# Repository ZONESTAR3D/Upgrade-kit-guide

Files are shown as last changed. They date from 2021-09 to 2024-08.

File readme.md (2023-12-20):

### :globe_with_meridians: Choose Language (Translated by google)
(https://github-com.translate.goog/ZONESTAR3D/Upgrade-kit-guide?_x_tr_sl=en&_x_tr_tl=es)
(https://github-com.translate.goog/ZONESTAR3D/Upgrade-kit-guide?_x_tr_sl=en&_x_tr_tl=pt)
(https://github-com.translate.goog/ZONESTAR3D/Upgrade-kit-guide?_x_tr_sl=en&_x_tr_tl=fr)
(https://github-com.translate.goog/ZONESTAR3D/Upgrade-kit-guide?_x_tr_sl=en&_x_tr_tl=de)
(https://github-com.translate.goog/ZONESTAR3D/Upgrade-kit-guide?_x_tr_sl=en&_x_tr_tl=it)
(https://github-com.translate.goog/ZONESTAR3D/Upgrade-kit-guide?_x_tr_sl=en&_x_tr_tl=sv)
(https://github-com.translate.goog/ZONESTAR3D/Upgrade-kit-guide?_x_tr_sl=en&_x_tr_tl=pl)
(https://github-com.translate.goog/ZONESTAR3D/Upgrade-kit-guide?_x_tr_sl=en&_x_tr_tl=da)
(https://github-com.translate.goog/ZONESTAR3D/Upgrade-kit-guide?_x_tr_sl=en&_x_tr_tl=cs)
(https://github-com.translate.goog/ZONESTAR3D/Upgrade-kit-guide?_x_tr_sl=en&_x_tr_tl=hr)
(https://github-com.translate.goog/ZONESTAR3D/Upgrade-kit-guide?_x_tr_sl=en&_x_tr_tl=ro)
(https://github-com.translate.goog/ZONESTAR3D/Upgrade-kit-guide?_x_tr_sl=en&_x_tr_tl=sk)

(https://github-com.translate.goog/ZONESTAR3D/Upgrade-kit-guide?_x_tr_sl=en&_x_tr_tl=ru)
(https://github-com.translate.goog/ZONESTAR3D/Upgrade-kit-guide?_x_tr_sl=en&_x_tr_tl=ja)
(https://github-com.translate.goog/ZONESTAR3D/Upgrade-kit-guide?_x_tr_sl=en&_x_tr_tl=ko)
(https://github-com.translate.goog/ZONESTAR3D/Upgrade-kit-guide?_x_tr_sl=en&_x_tr_tl=id)
(https://github-com.translate.goog/ZONESTAR3D/Upgrade-kit-guide?_x_tr_sl=en&_x_tr_tl=th)
(https://github-com.translate.goog/ZONESTAR3D/Upgrade-kit-guide?_x_tr_sl=en&_x_tr_tl=vi)
(https://github-com.translate.goog/ZONESTAR3D/Upgrade-kit-guide?_x_tr_sl=en&_x_tr_tl=iw)
(https://github-com.translate.goog/ZONESTAR3D/Upgrade-kit-guide?_x_tr_sl=en&_x_tr_tl=ar)
(https://github-com.translate.goog/ZONESTAR3D/Upgrade-kit-guide?_x_tr_sl=en&_x_tr_tl=tr)
(https://github-com.translate.goog/ZONESTAR3D/Upgrade-kit-guide?_x_tr_sl=en&_x_tr_tl=el)
(https://github-com.translate.goog/ZONESTAR3D/Upgrade-kit-guide?_x_tr_sl=en&_x_tr_tl=pt)
(https://github-com.translate.goog/ZONESTAR3D/Upgrade-kit-guide?_x_tr_sl=en&_x_tr_tl=zh-CN)

-----
# ZONESTAR 3D printer upgrade kits / parts 
## :file_folder: [Automatic Repeat Printing Module](./Auto_Repeat_Printing/) 
By upgrading this module to make your 3D printer capable of continuous automatic mass production, only for Z9 series 3d printers.   
[:book: **Use Guide**](./Auto_Repeat_Printing/readme.md)    
[:gift: **Sell Link**](https://www.aliexpress.com/item/1005003767078457.html) 

## :file_folder: [Bed Leveling Sensor](./Bed_Leveling_Sensor/)
[:book: **View details**](./Bed_Leveling_Sensor/)
Hot bed tilt / uneven surface is a common problem of 3D printer, however, the first layer is very important for the successfully print. The main solution to slove this problem is to use a ***bed leveling sensor*** to measure the distance between the nozzle with the hot bed, to generate a ***"hot bed height table"***, and save it in the memory of the 3D printer. While printing, automatically adjust the height of the nozzle to compensate the uneven hot bed. For more information on this issue, please refer to [**Marlin documents - Automatic Bed Leveling**](https://marlinfw.org/docs/features/auto_bed_leveling.html)    
**There are several types of bed leveling sensor:**      
- **PL-08N** is a proximity sensor, it can probing metal hotbed. If your hot bed surface is metal, such as aluminum plate + hot bed adhesive tape, aluminum plate + magnetic hot bed paste, elastic rigid hot bed, etc., you can use this sensor.[:gift: **Sell Link**](https://www.aliexpress.com/item/4000596309710.html)      
- **BLtouch(3DTouch)** is a "famous" bed auto leveling sensor for 3D Printers, it integrates a simple servo motor and an electromagnetic sensor into a very small volume. It can be used for all types of heat beds with high accuracy. The disadvantage is that the wiring and use are a little complex. [:gift: **Sell Link**](https://www.aliexpress.com/item/1005001464420529.html)   
- **ZL-Sensor** is a special photoelectric sensor made by ZONESTAR, it can probing almost all meterial hotbed, also it is easier to wiring such as PL-08N. [:gift: **Sell Link**](https://www.aliexpress.com/item/1005002865311470.html)  

## :file_folder: [Direct Drive Extruder](./Direct_Drive_Extruder/)
[:book: **View details**](./Direct_Drive_Extruder/)    
By using the direct drive extruder, the printer can print flexible filament (e.g. TPU filament) and get better printing quality.   
[:book: **Use Guide**](./Direct_Drive_Extruder/readme.md)   
[:gift: **Sell Link**](https://www.aliexpress.com/item/1005002847644867.html) 

## :file_folder: [Dual Gear Extruder](./Dual_Gear_Extruder/) 
The double gear extruder increases the force of filament feeding, which can effectively reduce the probability of printing defects and failures caused by filament slipping on the extruder.     
[:book: **View details**](./Dual_Gear_Extruder/)   
[:gift: **Full Metal Dual Gear Extruder**](https://www.aliexpress.com/item/1005005868564130.html) 
[:gift: **Dual Gear Extruder**](https://www.aliexpress.com/item/1005003473360998.html) 
[:gift: **4PCS/LOT Dual Gear Extruder**](https://www.aliexpress.com/item/1005006240027747.html) 

## :file_folder: [Filament Run Out Sensor (FROD)](./FROD/)
[:book:**View details**](./FROD/)
Filament run out sensor use a switch to check for the presence of filament in the feeder. If the filament spool runs out, the 3d printer will pause print and wait  you to replace a new spool.   
[**View details**](https://www.aliexpress.com/item/4001309957376.html)  

## :file_folder: [HOTENDs](./HOTEND/)
[:book: **View details**](./HOTEND/readme.md)  
ZONESTAR has been promoting the development of color FDM 3D printing technology, we have introduced different types of hot ends to meet the needs of multi-color printing.  
- **R3 (3-IN-3-OUT) Hotend**[:book: **Use Guide**](./HOTEND/R3/) [:gift: **Sell Link**](https://www.aliexpress.com/item/1005001275429959.html)  
- **M2P1 (3-IN-2-OUT Mix Color) Hotend**[:book: **Use Guide**](./HOTEND/M2P1/) [:gift: **Sell Link**](https://www.aliexpress.com/item/1005001275429959.html)  
- **M3 (3-IN-1-OUT Mix Color) Hotend**[:book: **Use Guide**](./HOTEND/M3/) [:gift: **Sell Link**](https://www.aliexpress.com/item/1005001275429959.html)  
- **M4 (4-IN-1-OUT Mix Color) Hotend**[:book: **Use Guide**](./HOTEND/M4/) [:gift: **Sell Link**](https://www.aliexpress.com/item/1005002124027691.html)  
- **E4 (4-IN-1-OUT Non-Mix Color) Hotend**[:book: **Use Guide**](./HOTEND/E4/) [:gift: **Sell Link**](https://www.aliexpress.com/item/1005002951777699.html)  

## :file_folder: [Laser Engraving](./Laser_Engraving/)
[:book: **View details**](./Laser_Engraving/)
By add a laser engrave engine , you can turn your 3D printer into a simple laser engraving machine.   
[:book: **Use Guide**](./Laser_Engraving/)   
[:gift: **Sell Link**](https://www.aliexpress.com/item/4001309902136.html)

## :file_folder: [Motor Drive Module](./Motor_Driver/)
[:book: **View details**](./Motor_Driver/)
TMC motor drive module used stealthChop2 ultra-quiet technology, it can After upgrading it, the noise of 3D printer stepper motor operation can be significantly reduced.   
[:book: **Use Guide**](./Motor_Driver/How_to_install_Motor_Driver_Module.pdf)  
[:gift: **TMC2208**](https://www.aliexpress.com/item/4000596369015.html) [:gift: **TMC2209**](https://www.aliexpress.com/item/1005001664336751.html) [:gift:**TMC2225**](https://www.aliexpress.com/item/1005003270721219.html)   

## :file_folder: [TFT-LCD](./TFT-LCD)
[:book: **View details**](./TFT-LCD/readme.md)    
[:gift: **Sell Link**](https://www.aliexpress.com/item/1005002378065646.html)  

## :file_folder: [WiFi Module](./WiFi/)
By upgrading the WiFi module, you can  control your 3d printer by wireless. It can work with ZM3E4 and ZM3E2 3D printer control board.   
<!-- [:book:**View details**](./WiFi/)     -->
[:book: **Use Guide**](./WiFi/WiFi_User_Guide.md)    
[:gift: **Sell Link**](https://www.aliexpress.com/item/1005002378551489.html)  

## :file_folder: [Z9V5 500x500 upgrade kit](./Z9V5_500x500/)
Upgrade the build volume of Z9V5 to 500x500x400mm.   
[:book: **View details**](./Z9V5_500x500/readme.md)     
[:gift :**Sell Link**](https://www.zonestar3dshop.com/products/zonestar-z9v5-500x500mm-large-printing-size-upgrade-kit-parts)  

## :file_folder: [Z9V5 linear rail upgrade kit](./Z9V5_LinearRail/)
Upgrade Z9V5 to linear rail.   
[:book: **View details**](./Z9V5_LinearRail/readme.md)     
[:gift: **Sell Link - Offical Store**](https://www.aliexpress.com/item/1005005599988527.html)  [:gift: **Sell Link - Aliexpress**](https://www.zonestar3dshop.com/products/new-arrival-z9v5pro-3d-printer-linear-rail-upgrade-kit-for-zonestar-z9v5pro-mgn9h-slider-3d-printer-parts)

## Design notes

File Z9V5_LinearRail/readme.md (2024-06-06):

### <a id="choose-language">:globe_with_meridians: Choose language </a>









<!-- [![](../lanpic/SW.png)](#sv)
[![](../lanpic/PL.png)](#pl)
[![](../lanpic/DK.png)](#da)
[![](../lanpic/CZ.png)](#cs)
[![](../lanpic/HR.png)](#hr)
[![](../lanpic/RO.png)](#ro)
[![](../lanpic/SK.png)](#sk)
[![](../lanpic/ID.png)](#id)
[![](../lanpic/TH.png)](#th)
[![](../lanpic/VN.png)](#vi)
[![](../lanpic/IL.png)](#iw)
[![](../lanpic/SA.png)](#ar)
[![](../lanpic/TR.png)](#tr)
[![](../lanpic/GR.png)](#el)
[![](../lanpic/BR.png)](#pt)
[![](../lanpic/CN.png)](#zh) -->

----
# <a id="en">Z9V5 Linear Rail Upgrade Kit Installation Guide</a>
### :warning: ATTENTION PLEASE :warning:
Do not slide the slider out of the linear rail, otherwise the balls will slide out of the slider and damage the slider.     
### Video Tutorial
(https://www.youtube.com/watch?v=YjfuKJFiPd4)

## Parts
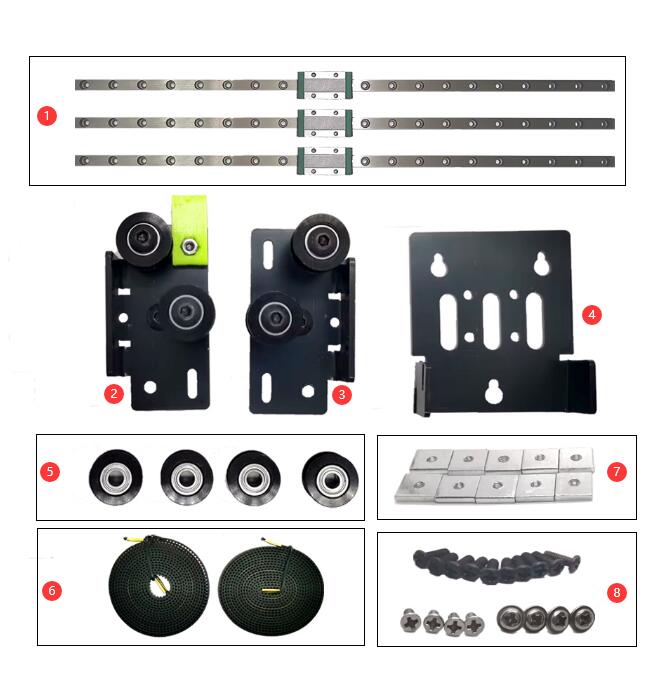
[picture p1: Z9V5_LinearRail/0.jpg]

>
    1. linear rail with slider    2. Y carrier(right)     3. Y carrier(left)      4. X Carrier Metal sheet
    5. Idlers                     6. Belts                7. 10x10 square nut     8. Screws

## Installation
### 1. Take down the hot end (print head) from the X carrier.
Loosen the screws which fixed the print head on the X carrier and take down the print head.   
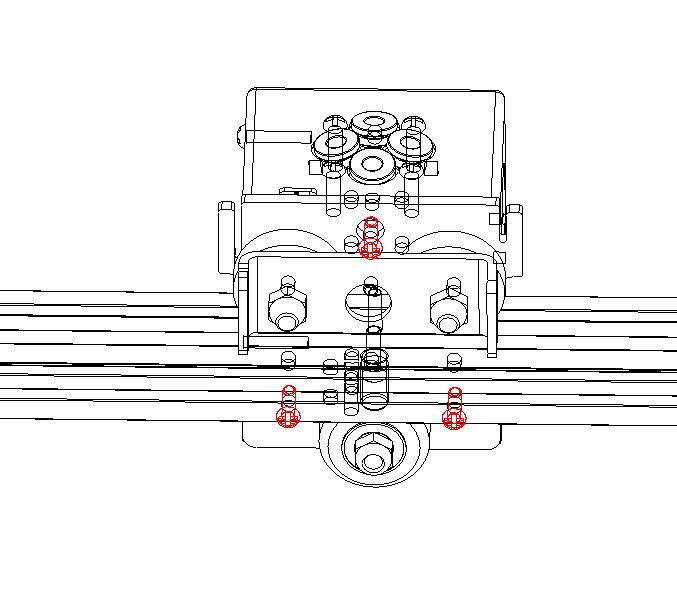
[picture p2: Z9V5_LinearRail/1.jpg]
###### 
### 2. Remove the belts.
### 3. Replace idlers.
Take down the idlers from the front-top profile and replace with the new idlers.    
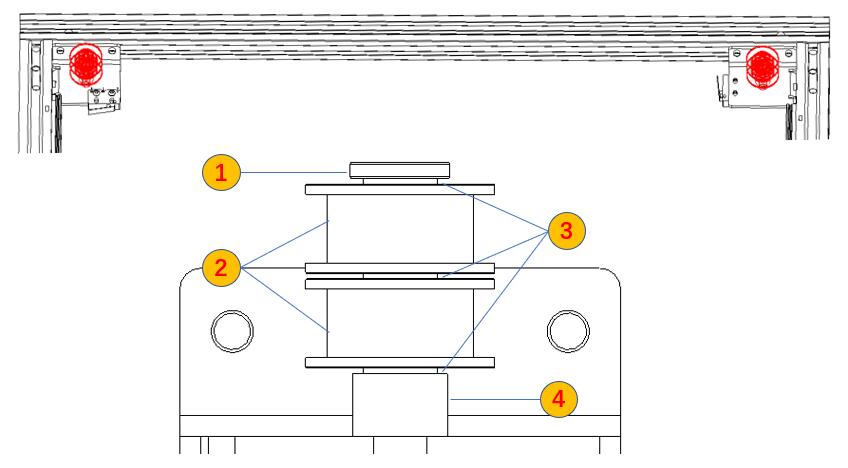
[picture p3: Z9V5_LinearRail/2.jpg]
###### 
>
    1. Screws (use the original one)     2. New idler wheels     3. New shim  4. Pole (use the orignal one)
  :warning: **Note:**
  - Do not tighten the screws too tightly.
  - There may be differences in the elevation columns of different versions of machines.

### 4. Take down the front-top profile.
Remove the screws shown on picture below to take down the front-top profile. **Note**the screw shown in Figure 3 only exists in the nearest Z9V5.  
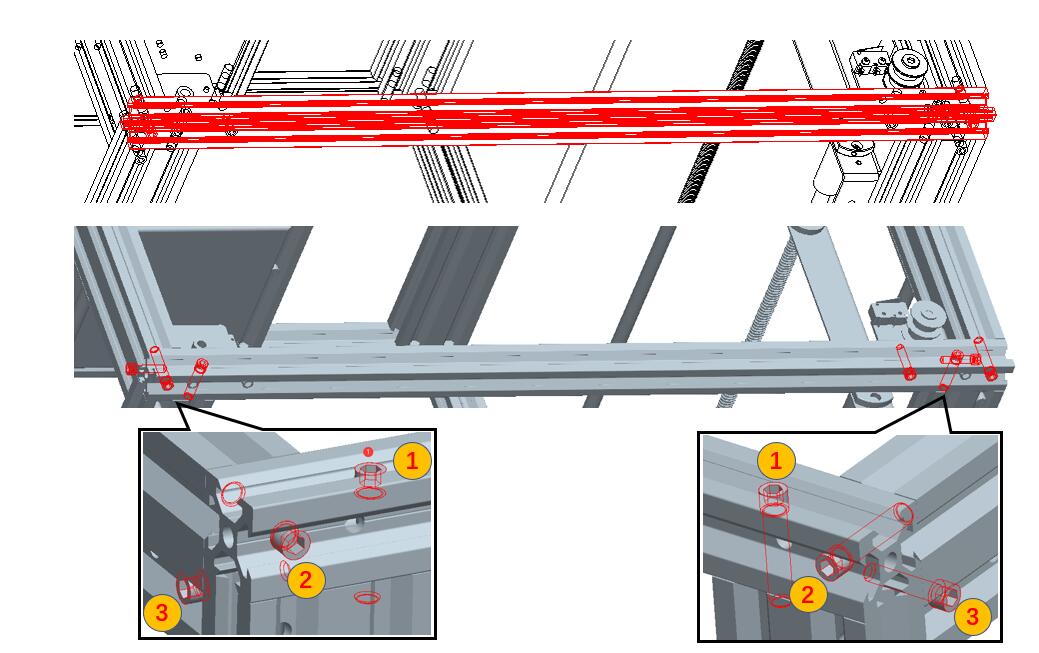
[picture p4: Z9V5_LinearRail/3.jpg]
###### 
### 5. Take down the X axis assembly.
### 6. Move the wires of X and Y ENDSTOPs from the top groove to the bottom groove of Y profiles.
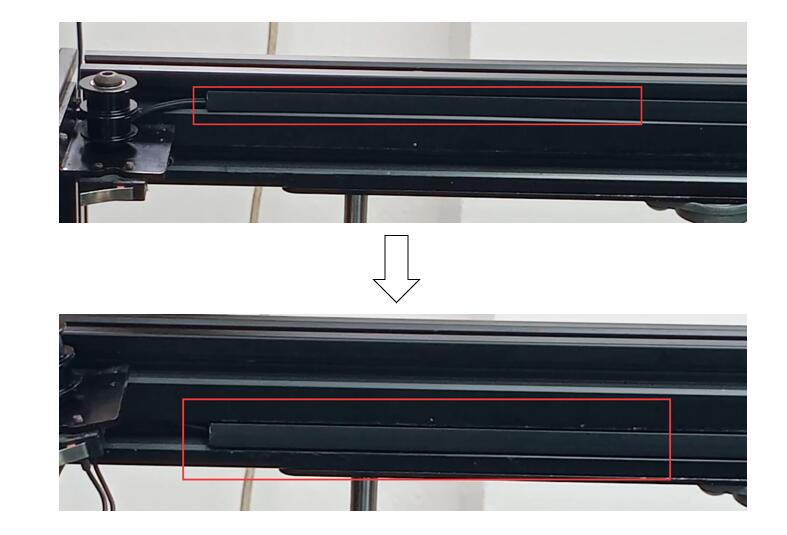
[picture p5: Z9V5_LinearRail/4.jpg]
###### 

### 7. Remove the original X and Y carrier from X axis assembly
#### 7.1 Take down the 4 screws which fixed the Y carriers to X profiles
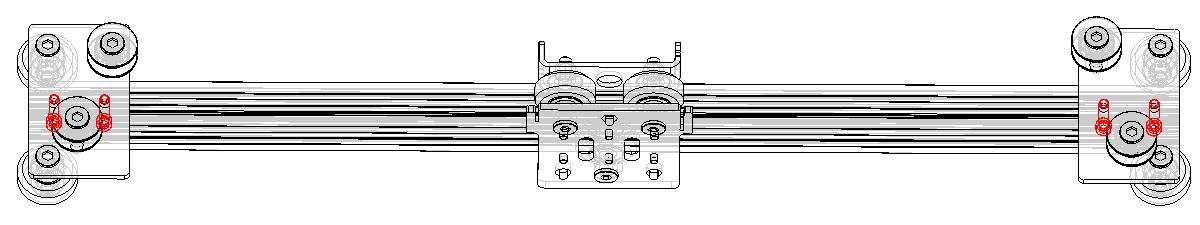
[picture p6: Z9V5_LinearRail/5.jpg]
###### 
#### 7.2 Take down X carriers from X profile.

### 8. Install a linear rail to the X profile.
  **:warning:Note: When installing the linear rail, do not let the slider slide out of the rail.**    
###### 
  - Install 3 pcs screws and 3 pcs square nuts to the linear guide rail.
  - Slide the linear guide rail from one side of the X profile, and place the square nut in the groove of the profile.
  - Roughly align at the middle of the linear rail and the X profile, and then fix the screws.
### 9. Install the new Y carriers (left and right) to the X profile.
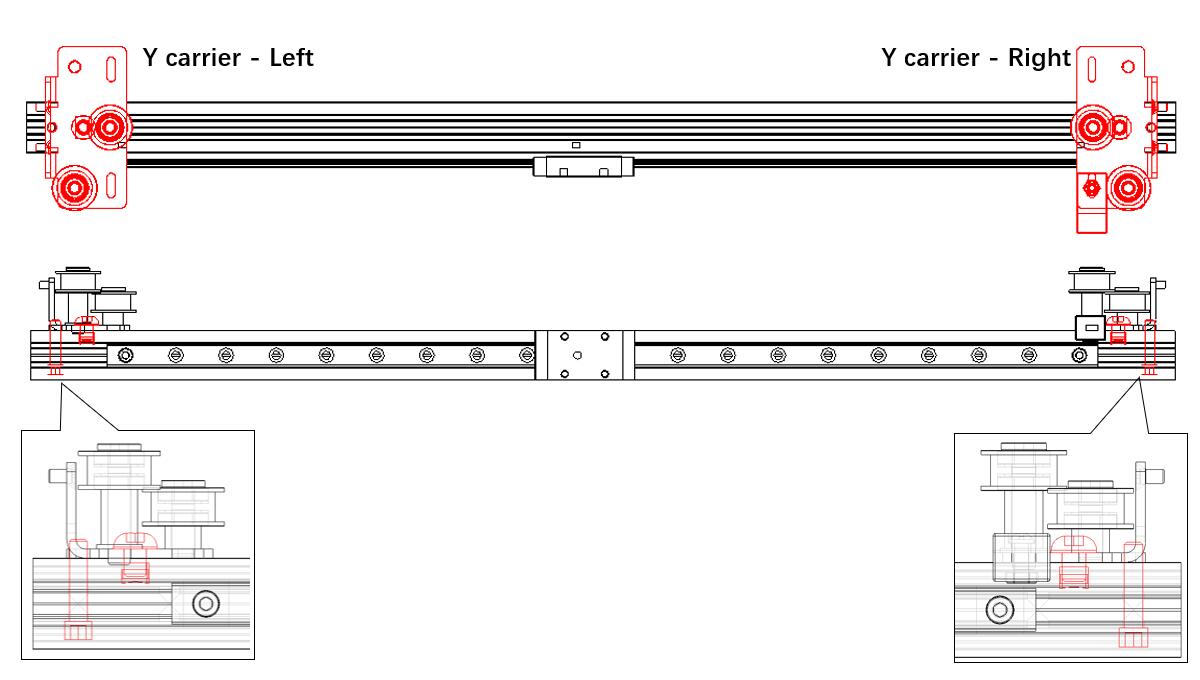
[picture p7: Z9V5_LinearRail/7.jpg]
###### 
  - Pay attention to differentiation left and right Y carrier, there is a plastic print on the right Y carrier.
  - The carrier is fixed by a M4 screw that has been removed from the bottom and a M5 screw with boat-nut installed on the sheet metal rom the top. When fixing the boat-nut, first rotate the screws counterclockwise for 2-3 turns, and then tighten by rotating clockwise. Do not tighten the screws too tightly at this step.
### 10 Install X carrier metal sheet to the silder of X linear rail.
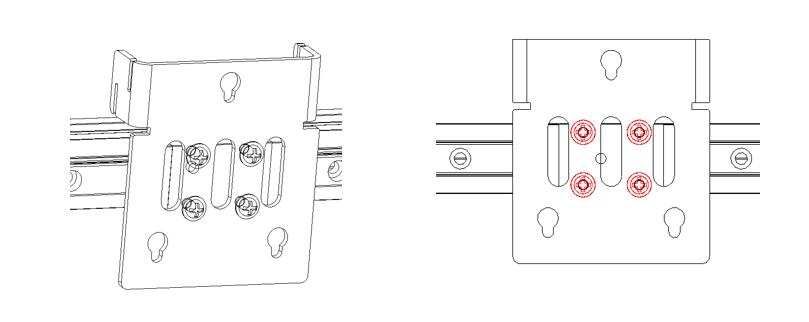
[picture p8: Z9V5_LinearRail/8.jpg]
###### 
### 11. Install linear rails to Y profile
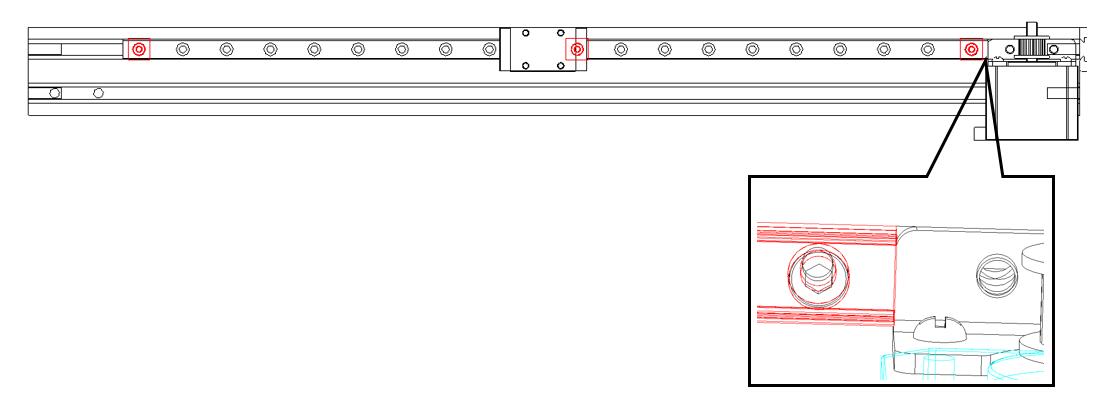
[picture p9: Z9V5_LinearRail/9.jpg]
###### 
  - Fix 3 screws and square nuts to the linear guide rail
  - Slide the linear guide rail from one side of the Y profile, and place the square nut in the **top groove** of the Y profile. 
  - Move the linear rail to the innermost of the Y profile (touched to the motor metla piece), and then fix the screw.
### 12 Reinstall the top-front profile back.
### 13 Install the X axis assembly to the sliders of Y carrier.
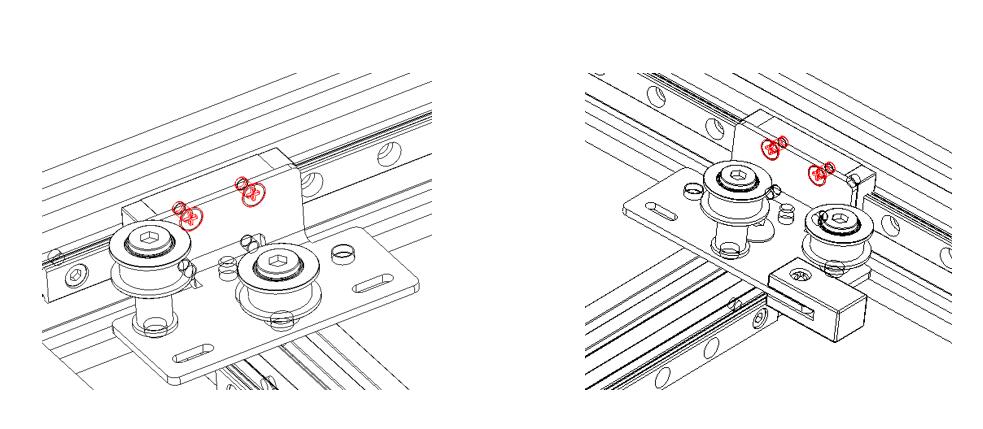
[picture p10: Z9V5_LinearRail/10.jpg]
###### 
:warning: Move the X-axis assembly to the end of the machine, align the left and right side Y carriers, and then tighten the screws that secure the Y-axis carriers.   
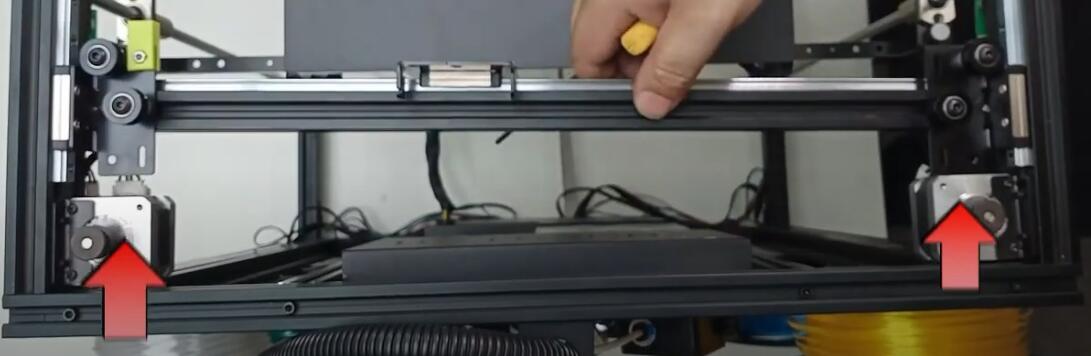
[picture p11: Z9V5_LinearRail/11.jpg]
###### 
### 14. Reinstall the hot end.
### 15. Install the new belts.

----
# <a id="es">Guía de instalación del kit de actualización de riel lineal Z9V5</a> [:arrow_heading_up:](#choose-language)
### :warning: ATENCIÓN POR FAVOR :warning:
No deslice el control deslizante fuera del riel lineal, de lo contrario las bolas se deslizarán fuera del control deslizante y dañarán el control deslizante.
### Vídeotutorial
(https://www.youtube.com/watch?v=YjfuKJFiPd4)

## Partes

>
 1. Riel lineal con deslizador 2. Soporte Y (derecha) 3. Soporte Y (izquierda) 4. Soporte X Chapa metálica
 5. Ruedas guía 6. Correas 7. Tuerca cuadrada de 10x10 8. Tornillos

## Instalación
### 1. Retire el extremo caliente (cabezal de impresión) del soporte X.
Afloje los tornillos que fijaron el cabezal de impresión en el soporte X y retire el cabezal de impresión.
###### 
### 2. Retire las correas.
### 3. Reemplace las poleas guía.
Retire las ruedas guía del perfil superior delantero y reemplácelas con ruedas guía nuevas.
###### 
>
 1. Tornillos (use el original) 2. Ruedas guía nuevas 3. Calza nueva 4. Poste (use el original)
 :warning: **Nota:**
 - No apretar demasiado los tornillos.
 - Pueden existir diferencias en las columnas de elevación de distintas versiones de máquinas.

### 4. Retire el perfil frontal superior.
Retire los tornillos que se muestran en la imagen a continuación para desmontar el perfil frontal superior. **Nota**El tornillo que se muestra en la Figura 3 solo existe en el Z9V5 más cercano.
###### 
### 5. Desmonte el conjunto del eje X.
### 6. Mueva los cables de los topes finales X e Y desde la ranura superior hasta la ranura inferior de los perfiles Y.
###### 

### 7. Retire los soportes X e Y originales del conjunto del eje X.
#### 7.1 Quitar los 4 tornillos que fijaban los soportes Y a los perfiles X
###### 
#### 7.2 Derribar X portadores del perfil X.

### 8. Instale un riel lineal en el perfil X.
 **:warning: Nota: Al instalar el riel lineal, no permita que el control deslizante se salga del riel.**
###### 
 - Instale 3 tornillos y 3 tuercas cuadradas en el riel guía lineal.
 - Deslizar el carril guía lineal desde un lado del perfil X, y colocar la tuerca cuadrada en la ranura del perfil.
 - Alinee aproximadamente en el centro del carril lineal y el perfil X, y luego fije los tornillos.
### 9. Instale los nuevos soportes Y (izquierdo y derecho) en el perfil X.
###### 
 - Preste atención a la diferenciación del soporte Y izquierdo y derecho, hay una impresión de plástico en el soporte Y derecho.
 - El soporte se fija mediante un tornillo M4 que se ha retirado de la parte inferior y un tornillo M5 con tuerca-barca instalado en la chapa de la parte superior. Al fijar la tuerca del barco, primero gire los tornillos en el sentido contrario a las agujas del reloj durante 2 o 3 vueltas y luego apriételos girándolos en el sentido de las agujas del reloj. No apriete demasiado los tornillos en este paso.
### 10 Instale la lámina metálica portadora X en el lado inferior del riel lineal X.
###### 
### 11. Instale los rieles lineales en el perfil Y
###### 
 - Fijar 3 tornillos y tuercas cuadradas al carril guía lineal.
 - Deslice el riel guía lineal desde un lado del perfil Y y coloque la tuerca cuadrada en la **ranura superior** del perfil Y.
 - Mueva el carril lineal hasta el interior del perfil Y (en contacto con la pieza metálica del motor) y luego fije el tornillo.
### 12 Vuelva a instalar el perfil frontal superior.
### 13 Instale el conjunto del eje X en los controles deslizantes del soporte Y.
###### 
:warning: Mueva el conjunto del eje X hasta el final de la máquina, alinee los soportes Y del lado izquierdo y derecho y luego apriete los tornillos que fijan los soportes del eje Y.
###### 
### 14. Reinstale el extremo caliente.
### 15. Instale las correas nuevas.

----
# <a id="pt">Guia de instalação do kit de atualização de trilho linear Z9V5</a> [:arrow_heading_up:](#choose-language)
### :warning: ATENÇÃO POR FAVOR :warning:
Não deslize o controle deslizante para fora do trilho linear, caso contrário as esferas deslizarão para fora do controle deslizante e danificarão o controle deslizante.
### Vídeo tutorial
(https://www.youtube.com/watch?v=YjfuKJFiPd4)

## Peças

>
 1. trilho linear com controle deslizante 2. Transportador Y (direita) 3. Transportador Y (esquerda) 4. Transportador X Folha de metal
 5. Rodas-guia 6. Correias 7. Porca quadrada 10x10 8. Parafusos

## Instalação
### 1. Retire o hot end (cabeça de impressão) do suporte X.
Afrouxe os parafusos que fixam a cabeça de impressão no suporte X e retire a cabeça de impressão.
###### 
### 2. Remova as correias.
### 3. Substitua os roletes.
Retire as rodas-guia do perfil frontal superior e substitua-as pelas novas rodas-guia.
###### 
>
 1. Parafusos (use o original) 2. Novas rodas intermediárias 3. Novo calço 4. Pólo (use o original)
 :warning: **Nota:**
 - Não aperte os parafusos com muita força.
 - Podem existir diferenças nas colunas de elevação das diferentes versões de máquinas.

### 4. Retire o perfil frontal superior.
Remova os parafusos mostrados na imagem abaixo para retirar o perfil frontal superior. **Observação**o parafuso mostrado na Figura 3 existe apenas no Z9V5 mais próximo.
###### 
### 5. Retire o conjunto do eixo X.
### 6. Mova os fios dos ENDSTOPs X e Y da ranhura superior para a ranhura inferior dos perfis Y.
###### 

### 7. Remova o suporte X e Y original do conjunto do eixo X
#### 7.1 Retire os 4 parafusos que fixam os suportes Y aos perfis X
###### 
#### 7.2 Remova as operadoras X do perfil X.

### 8. Instale um trilho linear no perfil X.
 **:warning:Nota: Ao instalar o trilho linear, não deixe o controle deslizante deslizar para fora do trilho.**
###### 
 - Instale 3 parafusos e 3 porcas quadradas no trilho-guia linear.
 - Deslize o trilho guia linear de um lado do perfil X e coloque a porca quadrada na ranhura do perfil.
 - Alinhe aproximadamente no meio do trilho linear e do perfil X e fixe os parafusos.
### 9. Instale os novos suportes Y (esquerdo e direito) no perfil X.
###### 
 - Preste atenção na diferenciação do suporte Y esquerdo e direito, há uma impressão plástica no suporte Y direito.
 - O suporte é fixado por um parafuso M4 que foi removido da parte inferior e um parafuso M5 com porca barco instalado na chapa pela parte superior. Ao fixar a porca barco, primeiro gire os parafusos no sentido anti-horário por 2-3 voltas e depois aperte girando no sentido horário. Não aperte os parafusos com muita força nesta etapa.
### 10 Instale a chapa metálica do suporte X na placa do trilho linear X.
###### 
### 11. Instale trilhos lineares no perfil Y
###### 
 - Fixe 3 parafusos e porcas quadradas no trilho-guia linear
 - Deslize o trilho-guia linear de um lado do perfil Y e coloque a porca quadrada na **ranhura superior** do perfil Y.
 - Mova o trilho linear até o ponto mais interno do perfil em Y (encostado na peça metálica do motor) e depois fixe o parafuso.
### 12 Reinstale o perfil frontal superior de volta.
### 13 Instale o conjunto do eixo X nos controles deslizantes do suporte Y.
###### 
:warning: Mova o conjunto do eixo X para a extremidade da máquina, alinhe os transportadores Y do lado esquerdo e direito e, em seguida, aperte os parafusos que prendem os transportadores do eixo Y.
###### 
### 14. Reinstale o hot end.
### 15. Instale as novas correias.

----
# <a id="fr">Guide d'installation du kit de mise à niveau du rail linéaire Z9V5</a> [:arrow_heading_up:](#choose-language)
### :warning: ATTENTION S'IL VOUS PLAÎT :warning:
Ne faites pas glisser le curseur hors du rail linéaire, sinon les billes glisseraient hors du curseur et endommageraient le curseur.
### Didacticiel vidéo
(https://www.youtube.com/watch?v=YjfuKJFiPd4)

## Les pièces

>
 1. rail linéaire avec curseur 2. Support Y (droite) 3. Support Y (gauche) 4. Support X Tôle
 5. Galets 6. Courroies 7. Écrou carré 10x10 8. Vis

##Installation
### 1. Retirez l'extrémité chaude (tête d'impression) du support X.
Desserrez les vis qui fixaient la tête d'impression sur le support X et démontez la tête d'impression.
###### 
### 2. Retirez les courroies.
### 3. Remplacez les rouleaux.
Retirez les rouleaux du profil supérieur avant et remplacez-les par les nouveaux rouleaux.
###### 
>
 1. Vis (utilisez celle d'origine) 2. Nouvelles roues folles 3. Nouvelle cale 4. Poteau (utilisez celle d'origine)
 :warning: **Remarque :**
 - Ne serrez pas trop les vis.
 - Il peut y avoir des différences dans les colonnes d'élévation des différentes versions de machines.

### 4. Retirez le profil supérieur avant.
Retirez les vis indiquées sur l'image ci-dessous pour démonter le profil avant supérieur. **Remarque**la vis illustrée sur la figure 3 n'existe que dans le Z9V5 le plus proche.
###### 
### 5. Démontez l'ensemble de l'axe X.
### 6. Déplacez les fils des butées X et Y de la rainure supérieure vers la rainure inférieure des profils Y.
###### 

### 7. Retirez les supports X et Y d'origine de l'assemblage de l'axe X
#### 7.1 Déposer les 4 vis qui fixaient les supports Y aux profilés X
###### 
#### 7.2 Supprimez les transporteurs X du profil X.

### 8. Installez un rail linéaire sur le profil X.
 **:warning: Remarque: lors de l'installation du rail linéaire, ne laissez pas le curseur glisser hors du rail.**
###### 
 - Installez 3 vis et 3 écrous carrés sur le rail de guidage linéaire.
 - Faites glisser le rail de guidage linéaire d'un côté du profilé X, et placez l'écrou carré dans la rainure du profilé.
 - Alignez grossièrement le milieu du rail linéaire et le profilé X, puis fixez les vis.

### 9. Installez les nouveaux supports Y (gauche et droit) sur le profil X.
###### 
 - Faites attention à la différenciation du support Y gauche et droit, il y a une impression plastique sur le support Y droit.
 - Le support est fixé par une vis M4 retirée par le bas et une vis M5 avec écrou bateau installée sur la tôle par le haut. Lors de la fixation de l'écrou bateau, faites d'abord tourner les vis dans le sens inverse des aiguilles d'une montre pendant 2 à 3 tours, puis serrez en les tournant dans le sens des aiguilles d'une montre. Ne serrez pas trop les vis à cette étape.

### 10 Installez la tôle de support X sur le support du rail linéaire X.
###### 

### 11. Installez les rails linéaires sur le profil Y
###### 
 - Fixer 3 vis et écrous carrés au rail de guidage linéaire
 - Faites glisser le rail de guidage linéaire d'un côté du profilé Y et placez l'écrou carré dans la **rainure supérieure** du profilé Y.
 - Déplacez le rail linéaire vers l'intérieur du profil Y (en contact avec la pièce métallique du moteur), puis fixez la vis.
### 12 Réinstallez le profil supérieur avant.

### 13 Installez l'ensemble de l'axe X sur les curseurs du support Y.
###### 
:warning: déplacez l'ensemble de l'axe X jusqu'à l'extrémité de la machine, alignez les supports Y latéraux gauche et droit, puis serrez les vis qui fixent les supports de l'axe Y.

###### 
### 14. Réinstallez le hot end.
### 15. Installez les nouvelles courroies.

----
# <a id="de">Installationsanleitung für das Upgrade-Kit für die Z9V5-Linearschiene</a> [:arrow_heading_up:](#choose-language)
### :warning: ACHTUNG BITTE :warning:
Schieben Sie den Schieber nicht aus der Linearschiene heraus, da sonst die Kugeln aus dem Schieber herausrutschen und den Schieber beschädigen.
### Video-Tutorial
(https://www.youtube.com/watch?v=YjfuKJFiPd4)

## Teile

>
1. Linearschiene mit Schieber 2. Y-Träger (rechts) 3. Y-Träger (links) 4. X-Träger Metallblech
5. Spannrollen 6. Riemen 7. 10x10 Vierkantmutter 8. Schrauben

## Installation
### 1. Nehmen Sie das Hot-End (Druckkopf) vom X-Träger ab.
Lösen Sie die Schrauben, mit denen der Druckkopf am X-Träger befestigt ist, und nehmen Sie den Druckkopf ab.
###### 
### 2. Entfernen Sie die Riemen.
### 3. Ersetzen Sie die Spannrollen.
Nehmen Sie die Spannrollen vom vorderen oberen Profil ab und ersetzen Sie sie durch die neuen Spannrollen.
###### 
>
1. Schrauben (verwenden Sie die Originalschrauben) 2. Neue Spannrollen 3. Neue Unterlegscheibe 4. Stange (verwenden Sie die Originalschrauben)
:warning: **Hinweis:**
- Ziehen Sie die Schrauben nicht zu fest an.
- Es kann Unterschiede in den Höhensäulen verschiedener Maschinenversionen geben.

### 4. Nehmen Sie das vordere obere Profil ab.
Entfernen Sie die auf dem Bild unten gezeigten Schrauben, um das vordere obere Profil abzunehmen. **Hinweis** Die in Abbildung 3 gezeigte Schraube ist nur im nächsten Z9V5 vorhanden.
###### 
### 5. Bauen Sie die X-Achsen-Baugruppe ab.
### 6. Verlegen Sie die Drähte der X- und Y-ENDSTOPs von der oberen Nut zur unteren Nut der Y-Profile.
###### 

### 7. Entfernen Sie den ursprünglichen X- und Y-Träger von der X-Achsen-Baugruppe
#### 7.1 Entfernen Sie die 4 Schrauben, mit denen die Y-Träger an den X-Profilen befestigt sind
###### 
#### 7.2 Entfernen Sie die X-Träger vom X-Profil.

### 8. Installieren Sie eine Linearschiene am X-Profil.
**:warning:Hinweis: Lassen Sie beim Installieren der Linearschiene den Schieber nicht aus der Schiene gleiten.**
###### 
- Installieren Sie 3 Schrauben und 3 Vierkantmuttern an der Linearführungsschiene.
- Schieben Sie die lineare Führungsschiene von einer Seite des X-Profils und platzieren Sie die Vierkantmutter in der Nut des Profils.
- Richten Sie die Mitte der linearen Schiene und des X-Profils grob aus und ziehen Sie dann die Schrauben fest.

### 9. Installieren Sie die neuen Y-Träger (links und rechts) am X-Profil.
###### 
- Achten Sie auf die Unterscheidung zwischen linkem und rechtem Y-Träger, auf dem rechten Y-Träger befindet sich ein Kunststoffaufdruck.
- Der Träger wird durch eine M4-Schraube befestigt, die von unten entfernt wurde, und eine M5-Schraube mit Bootsmutter, die von oben auf dem Blech angebracht ist. Drehen Sie beim Anbringen der Bootsmutter die Schrauben zunächst 2-3 Umdrehungen gegen den Uhrzeigersinn und ziehen Sie sie dann durch Drehen im Uhrzeigersinn fest. Ziehen Sie die Schrauben bei diesem Schritt nicht zu fest an.

### 10 Installieren Sie das Metallblech des X-Trägers an der Seite der linearen X-Schiene.
###### 

### 11. Linearschienen am Y-Profil anbringen
####### 
- 3 Schrauben und Vierkantmuttern an der Linearführungsschiene anbringen
- Die Linearführungsschiene von einer Seite des Y-Profils einschieben und die Vierkantmutter in die **obere Nut** des Y-Profils einsetzen.
- Die Linearschiene ganz nach innen in das Y-Profil schieben (bis sie das Metallteil des Motors berührt) und dann die Schraube anziehen.

### 12 Das obere vordere Profil wieder anbringen.
### 13 Die X-Achsenbaugruppe an den Gleitstücken des Y-Trägers anbringen.
###### 
:warning: Die X-Achsenbaugruppe an das Ende der Maschine anbringen, die linken und rechten Y-Träger ausrichten und dann die Schrauben festziehen, die die Y-Achsenträger sichern.
###### 
### 14. Bauen Sie das Hot-End wieder ein.
### 15. Bauen Sie die neuen Riemen ein.

----
# <a id="it">Guida all'installazione del kit di aggiornamento della guida lineare Z9V5</a> [:arrow_heading_up:](#choose-language)
### :warning: ATTENZIONE PER FAVORE :warning:
Non far scorrere il cursore fuori dalla guida lineare, altrimenti le sfere scivoleranno fuori dal cursore e danneggeranno il cursore.
### Videotutorial
(https://www.youtube.com/watch?v=YjfuKJFiPd4)

## Parti

>
 1. guida lineare con cursore 2. Carrello Y (destra) 3. Carrello Y (sinistra) 4. Carrello X Lamiera metallica
 5. Tenditori 6. Cinghie 7. Dado quadro 10x10 8. Viti

## Installazione
### 1. Rimuovere l'hot end (testina di stampa) dal supporto X.
Allentare le viti che fissavano la testina di stampa sul supporto X e smontare la testina di stampa.
###### 
### 2. Rimuovere le cinghie.
### 3. Sostituire i tenditori.
Rimuovere le tenditrici dal profilo superiore anteriore e sostituirle con le nuove tenditrici.
###### 
>
 1. Viti (usare quella originale) 2. Nuove ruote tenditrici 3. Nuovo spessore 4. Palo (usare quello originale)
 :warning: **Nota:**
 - Non stringere troppo le viti.
 - Potrebbero esserci differenze nelle colonne di elevazione delle diverse versioni delle macchine.

### 4. Smontare il profilo anteriore-superiore.
Rimuovere le viti mostrate nella figura sotto per smontare il profilo superiore anteriore. **Nota**la vite mostrata nella Figura 3 esiste solo nel Z9V5 più vicino.
###### 
### 5. Rimuovere il gruppo dell'asse X.
### 6. Spostare i fili dei ENDSTOP X e Y dalla scanalatura superiore alla scanalatura inferiore dei profili Y.
###### 

### 7. Rimuovere il supporto X e Y originale dal gruppo dell'asse X
#### 7.1 Togliere le 4 viti che fissavano i supporti Y ai profili X
###### 
#### 7.2 Elimina i vettori X dal profilo X.

### 8. Installare una guida lineare sul profilo X.
 **:warning: Nota: durante l'installazione della guida lineare, non lasciare che il cursore scivoli fuori dalla guida.**
###### 
 - Installare 3 viti e 3 dadi quadrati sulla guida lineare.
 - Far scorrere la guida lineare da un lato del profilo X e posizionare il dado quadrato nella scanalatura del profilo.
 - Allineare approssimativamente al centro della guida lineare e del profilo X, quindi fissare le viti.
### 9. Installare i nuovi supporti Y (sinistro e destro) sul profilo X.
###### 
 - Prestare attenzione alla differenziazione del supporto Y sinistro e destro, sul supporto Y destro è presente una stampa in plastica.
 - Il supporto è fissato tramite una vite M4 rimossa dal fondo e una vite M5 con dado a barca installata sulla lamiera dalla parte superiore. Quando si fissa il dado della barca, ruotare prima le viti in senso antiorario per 2-3 giri, quindi serrarle ruotandole in senso orario. Non stringere troppo le viti in questa fase.
### 10 Installare la lamiera metallica del supporto X sul rivestimento della guida lineare X.
###### 
### 11. Installare le guide lineari sul profilo Y
###### 
 - Fissare 3 viti e dadi quadrati alla guida lineare
 - Far scorrere la guida lineare da un lato del profilo Y e posizionare il dado quadrato nella **scanalatura superiore** del profilo Y.
 - Spostare la guida lineare nella parte più interna del profilo Y (toccata sul pezzo metallico del motore), quindi fissare la vite.
### 12 Reinstallare nuovamente il profilo anteriore superiore.
### 13 Installare il gruppo dell'asse X sui cursori del supporto Y.
###### 
:warning: spostare il gruppo dell'asse X all'estremità della macchina, allineare i supporti Y del lato sinistro e destro, quindi serrare le viti che fissano i supporti dell'asse Y.
###### 
### 14. Reinstallare l'hot-end.
### 15. Installare le nuove cinghie.

----
# <a id="ru">Руководство по установке комплекта обновления линейной направляющей Z9V5</a> [:arrow_heading_up:](#choose-language)
### :warning: ВНИМАНИЕ :warning:
Не выдвигайте ползунок из линейной направляющей, иначе шарики выскользнут из ползунка и повредят его.
### Видеоурок
(https://www.youtube.com/watch?v=YjfuKJFiPd4)

## Детали

>
 1. Линейная направляющая с ползунком 2. Держатель Y (справа) 3. Держатель Y (слева) 4. Держатель X Металлический лист
 5. Натяжные ролики 6. Ремни 7. Квадратная гайка 10х10 8. Винты

## Монтаж
### 1. Снимите горячий конец (печатающую головку) с держателя X.
Ослабьте винты, которые фиксируют печатающую головку на держателе X, и снимите печатающую головку.
###### 
### 2. Снимите ремни.
### 3. Замените натяжные ролики.
Снимите натяжные ролики с переднего верхнего профиля и замените их новыми.
###### 
>
 1. Винты (используйте оригинальные) 2. Новые натяжные колеса 3. Новая прокладка 4. Полюс (используйте оригинальную)
 :warning: **Примечание:**
 - Не затягивайте винты слишком сильно.
 - Могут быть различия в высоте столбцов разных версий машин.

### 4. Снимите передний верхний профиль.
Удалите винты, показанные на рисунке ниже, чтобы снять передний верхний профиль. **Обратите внимание**, что винт, показанный на рисунке 3, имеется только в ближайшем Z9V5.
###### 
### 5. Снимите узел оси X.
### 6. Переместите провода концевых упоров X и Y из верхнего паза в нижний паз Y-профиля.
###### 

### 7. Снимите исходный суппорт X и Y с узла оси X.
#### 7.1 Открутите 4 винта, которыми держатели Y крепятся к профилям X.
###### 
#### 7.2 Удалить X операторов связи из X профиля.

### 8. Установите линейную направляющую на X-профиль.
 **:warning:Примечание. При установке линейной направляющей не допускайте выскальзывания ползунка из направляющей.**
###### 
 - Установите 3 винта и 3 квадратных гайки на линейную направляющую.
 - Сдвиньте линейную направляющую с одной стороны X-профиля и поместите квадратную гайку в паз профиля.
 - Примерно совместите середину линейной направляющей и X-профиля, а затем закрепите винты.
### 9. Установите новые держатели Y (слева и справа) в профиль X.
###### 
 - Обратите внимание на различение левого и правого держателя Y, на правом держателе Y имеется пластиковая печать.
 - Держатель крепится винтом М4, снятым снизу, и винтом М5 с лодочной гайкой, установленным на листовом металле сверху. При фиксации гайки-лодочки сначала поверните винты против часовой стрелки на 2-3 оборота, а затем затяните, вращая их по часовой стрелке. На этом этапе не затягивайте винты слишком сильно.
### 10 Установите металлический лист несущей X на золотник линейного рельса X.
###### 
### 11. Установите линейные направляющие на Y-профиль.
###### 
 - Закрепите 3 винта и квадратные гайки на линейной направляющей.
 - Сдвиньте линейную направляющую с одной стороны Y-профиля и поместите квадратную гайку в **верхний паз** Y-профиля.
 - Переместите линейную направляющую к самой внутренней части Y-профиля (прикасаясь к металлическому элементу двигателя), а затем закрепите винт.
###12 Установите верхний передний профиль обратно.
### 13 Установите узел оси X на ползунки держателя Y.
###### 
:warning: Переместите узел оси X в конец машины, выровняйте левую и правую стороны держателей Y, а затем затяните винты, крепящие держатели оси Y.
###### 
### 14. Переустановите хотэнд.
### 15. Установите новые ремни.

----
# <a id="jp">Z9V5 リニア レール アップグレード キット インストール ガイド</a>  [:arrow_heading_up:](#choose-language)
### :warning: ご注意ください :warning:
スライダーをリニア レールからスライドさせないでください。そうしないと、ボールがスライダーからスライドし、スライダーが損傷します。
### ビデオ チュートリアル
(https://www.youtube.com/watch?v=YjfuKJFiPd4)

## パーツ

>
1. スライダー付きリニア レール 2. Y キャリア (右) 3. Y キャリア (左) 4. X キャリア 金属シート
5. アイドラー 6. ベルト 7. 10x10 角ナット 8. ネジ

## インストール
### 1. ホット エンド (プリント ヘッド) を X キャリアから取り外します。
プリントヘッドを X キャリアに固定しているネジを緩めて、プリントヘッドを取り外します。
###### 
### 2. ベルトを取り外します。
### 3. アイドラーを交換します。
フロントトップ プロファイルからアイドラーを取り外し、新しいアイドラーと交換します。
###### 
>
1. ネジ (元のものを使用) 2. 新しいアイドラー ホイール 3. 新しいシム 4. ポール (元のものを使用)
:warning: **注意:**
- ネジを締めすぎないでください。
- マシンのバージョンによって、仰角の柱が異なる場合があります。

### 4. フロントトップ プロファイルを取り外します。
フロントトップ プロファイルを外すには、下の写真に示されているネジを取り外します。**注意**図 3 に示されているネジは、最も近い Z9V5 にのみ存在します。
###### 
### 5. X 軸アセンブリを取り外します。
### 6. X および Y エンドストップのワイヤを Y プロファイルの上部の溝から下部の溝に移動します。
##### 

### 7. X 軸アセンブリから元の X および Y キャリアを取り外します
#### 7.1 Y キャリアを X プロファイルに固定している 4 本のネジを取り外します
###### 
#### 7.2 X プロファイルから X キャリアを取り外します。

### 8. X プロファイルにリニア レールを取り付けます。
**:warning:注意: リニア レールを取り付けるときは、スライダーがレールから滑り出さないようにしてください。**
###### 
- リニア ガイド レールに 3 本のネジと 3 個の四角ナットを取り付けます。
- リニアガイドレールをXプロファイルの片側からスライドさせ、四角ナットをプロファイルの溝に置きます。
- リニアレールとXプロファイルの中央を大まかに揃えてから、ネジを固定します。
### 9. 新しいYキャリア（左と右）をXプロファイルに取り付けます。
###### 
- 左と右のYキャリアを区別することに注意してください。右のYキャリアにはプラスチックのプリントがあります。
- キャリアは、下部から取り外したM4ネジと、上からシートメタルに取り付けられたボートナット付きのM5ネジで固定されています。ボートナットを固定するときは、最初にネジを反時計回りに2〜3回転してから、時計回りに回して締めます。この手順では、ネジを締めすぎないようにしてください。
### 10 XリニアレールのサイドにXキャリアメタルシートを取り付けます。
###### 
### 11. リニア レールを Y プロファイルに取り付けます
###### 
- 3 本のネジと四角ナットをリニア ガイド レールに固定します
- リニア ガイド レールを Y プロファイルの片側からスライドさせ、四角ナットを Y プロファイルの **上部の溝** に配置します。
- リニア レールを Y プロファイルの最も内側 (モーター メトラ ピースに接触) に移動し、ネジを固定します。
### 12 トップフロント プロファイルを再度取り付けます。
### 13 X 軸アセンブリを Y キャリアのスライダーに取り付けます。
###### 
:warning: X 軸アセンブリをマシンの端に移動し、左側と右側の Y キャリアを揃えてから、Y 軸キャリアを固定するネジを締めます。
###### 
### 14. ホットエンドを再度取り付けます。
### 15. 新しいベルトを取り付けます。

----
# <a id="kr">Z9V5 선형 레일 업그레이드 키트 설치 안내서</a> [:arrow_heading_up:](#choose-language)
### :warning: 주의하세요 :warning:
슬라이더를 선형 레일 밖으로 밀어내지 마십시오. 그렇지 않으면 볼이 슬라이더 밖으로 미끄러져 나와 슬라이더가 손상될 수 있습니다.
### 비디오 튜토리얼
(https://www.youtube.com/watch?v=YjfuKJFiPd4)

## 부속

>
 1. 슬라이더가 있는 선형 레일 2. Y 캐리어(오른쪽) 3. Y 캐리어(왼쪽) 4. X 캐리어 금속 시트
 5. 아이들러 6. 벨트 7. 10x10 사각 너트 8. 나사

## 설치
### 1. X 캐리어에서 핫엔드(프린트 헤드)를 떼어냅니다.
X 캐리어의 프린트 헤드를 고정한 나사를 풀고 프린트 헤드를 아래로 내립니다.
###### 
### 2. 벨트를 제거합니다.
### 3. 아이들러를 교체하세요.
전면 상단 프로파일에서 아이들러를 제거하고 새 아이들러로 교체합니다.
###### 
>
 1. 나사(원래 것을 사용) 2. 새 아이들러 휠 3. 새 심 4. 폴(원래 것을 사용)
 :warning: **참고:**
 - 나사를 너무 세게 조이지 마십시오.
 - 기계 버전에 따라 고도 열에 차이가 있을 수 있습니다.

### 4. 전면 상단 프로필을 내립니다.
아래 그림에 표시된 나사를 제거하여 전면 상단 프로파일을 아래로 내립니다. **참고**그림 3에 표시된 나사는 가장 가까운 Z9V5에만 있습니다.
###### 
### 5. X축 어셈블리를 분해합니다.
### 6. X 및 Y ENDSTOP의 와이어를 상단 홈에서 Y 프로파일의 하단 홈으로 이동합니다.
###### 

### 7. X축 어셈블리에서 원래 X 및 Y 캐리어를 제거합니다.
#### 7.1 Y 캐리어를 X 프로파일에 고정한 4개의 나사를 풀어냅니다.
###### 
#### 7.2 X 프로필에서 X 캐리어를 제거합니다.

### 8. X 프로파일에 선형 레일을 설치합니다.
 **:warning: 참고: 선형 레일을 설치할 때 슬라이더가 레일 밖으로 미끄러지지 않도록 하십시오.**
###### 
 - 선형 가이드 레일에 나사 3개와 사각 너트 3개를 설치합니다.
 - X 프로파일의 한쪽 측면에서 선형 가이드 레일을 밀고 사각 너트를 프로파일의 홈에 놓습니다.
 - 리니어 레일과 X 프로파일의 중앙을 대략적으로 맞춘 후 나사를 고정합니다.
### 9. 새 Y 캐리어(왼쪽 및 오른쪽)를 X 프로파일에 설치합니다.
###### 
 - 왼쪽과 오른쪽 Y 캐리어 구별에 주의하세요. 오른쪽 Y 캐리어에 플라스틱 프린트가 있습니다.
 - 캐리어는 하단에서 제거된 M4 나사와 상단에서 판금에 설치된 보트 너트가 있는 M5 나사로 고정됩니다. 보트 너트를 고정할 때에는 먼저 나사를 시계 반대 방향으로 2~3바퀴 돌린 후 시계 방향으로 돌려 조여줍니다. 이 단계에서 나사를 너무 세게 조이지 마십시오.
### 10 X 리니어 레일의 실버에 X 캐리어 메탈 시트를 설치합니다.
###### 
### 11. Y 프로파일에 선형 레일 설치
###### 
 - 리니어 가이드 레일에 나사 3개와 사각 너트를 고정합니다.
 - Y 프로파일의 한쪽에서 선형 가이드 레일을 밀고 Y 프로파일의 **상단 홈**에 사각형 너트를 놓습니다.
 - 선형 레일을 Y 프로파일의 가장 안쪽(모터 금속 조각에 닿음)으로 이동시킨 후 나사를 고정합니다.
### 12 상단 전면 프로파일을 다시 설치하세요.
### 13 X축 어셈블리를 Y캐리어의 슬라이더에 설치합니다.
###### 
:warning: X축 어셈블리를 기계 끝으로 이동하고 왼쪽 및 오른쪽 Y 캐리어를 맞춘 다음 Y축 캐리어를 고정하는 나사를 조입니다.
###### 
### 14. 핫엔드를 다시 설치합니다.
### 15. 새 벨트를 설치합니다.

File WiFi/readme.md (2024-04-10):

### By upgrading the WiFi module, you can control your 3d printer by wireless. It can work with ZONESTAR Z9V5, Z9M4, Z8P 3D Printer or the others 3d printer used ZONESTAR ZM3E4 and ZM3E2 32-bits 3D printer control board.
[**:gift: Buy it from ZONESTAR Online Shop**](https://bit.ly/3rB7mx1)
[**:gift: Buy it from Aliexpress Offical Shop**](https://bit.ly/3i7aX4o)

## User guide
:book: [User guide](./WiFi_User_Guide.md)  
:green_book: [User guide pdf file](./WiFi_User_Guide.pdf)  

## Install WiFi module (click the below link and then click download button to download)
### For Z8PM4 
Open the control box and install WiFi module.         
[:clapper: :arrow_down: Download the video tutorial](./Install_WiFi_Z8P.mp4)
### For Z9V5
Open control box and then install the WiFi module to the control board.       
[:art: Picture of how to open the Z9V5Pro's control box](./How_to_open_the_control_box_Z9V5.jpg)            
[:clapper: Open the Z9V5Pro's control box](./Open_the_Control_Box_of_Z9V5.gif)    
[:clapper: Install the WiFi module](./Install_WiFi_Z9V5.gif)

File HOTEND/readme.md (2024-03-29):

# Hotend
The hotend is the component of a extruder of the FDM 3D printer that melts the filament. Generally, a hot end consists of the following parts:
1. **Nozzle**: To melt filament and flow out，the size of its outlet determines the layer thickness can be built. It is usually made of materials with high thermal conductivity and high hardness, such as copper, carbon steel.  
2. **Heating block**: It is a device to fix the heater and nozzle together. It is usually made of materials with high thermal conductivity, such as aluminum and copper. In some designs, the nozzle and heating block may be integrated.
3. **Heat break**: It is a device used to isolate the heater from the printer, usually made of high temperature resistant but low thermal conductivity materials, such as stainless steel, PEEK, titanium, etc..  
4. **Heat sink**: In order to fix the hot end and keep the filaments cool in front of the hot end to conduct extrusion pressure, the heat break usually needs to be connected to a heat sink, and then install the heat sink to the 3d printer.    
5. **Cooling fan**: Speed up the heat dissipation efficiency of the heat sink, and there are also designs using water cooling methods.  
6. **Extruder fan**: It be used to cool the colloid flowed out from the nozzle so that the filaments can be formed and fixed ASAP.  
7. **Heater**: It be used to heat the nozzle, usually using a 40W~60W cartridge heater.
8. **Temperature sensor**: For measuring the temperature of the hot block (nozzle).
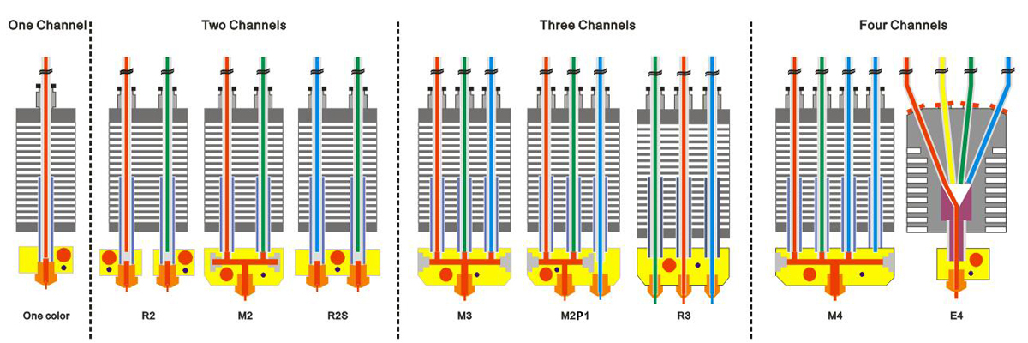
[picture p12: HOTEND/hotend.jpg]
      
:link: **Referance document @ Reprap: [Hot End Design Theory](https://reprap.org/wiki/Hot_End_Design_Theory)**      

------
## 4 Channels Hotend
### :file_folder: [E4 (4-IN-1-OUT Non-Mix Color) Hotend](./E4/)
**E4 hotend** is a 4-IN-1-OUT non-mix color hotend, it has four input channels and one nozzle. One of the four filaments can be loaded into the heating block and extruded through the nozzle. When a new filament loaded in, it needs to unload the previous filament first.  
For details, please refer to [**here**](./E4/readme.md).  

### :file_folder: [M4 (4-IN-1-OUT Mix color) Hotend](./M4/)
**M4 hotend** is a 4-IN-1-OUT mix color hotend, it has four input channels and one nozzle. The filaments are mixed in the heating block and extruded through the nozzle.   
For details, please refer to [**here**](./M4/readme.md). 

### :file_folder: [FAQ for E4 and M4 Hotend](./FAQ_M4E4.md)
- [**What's the different between E4 and M4 hotend?**](./FAQ_M4E4.md)
- [**Which type of hotend should I choose?**](./FAQ_M4E4.md)
- [**How to load filaments into the hotend correctly?**](./FAQ_M4E4.md)
- [**What is the difference in slicing settings between M4 and E4 hotends**](./FAQ_M4E4.md)
- [**How to switch between M4 and E4 hotend?**](./FAQ_M4E4.md)

------
## 3 Channels Hotend
### :file_folder: [M3 (3-IN-1-OUT Mix color) Hotend](./M3/)
**M3** hot end is a 3-IN-1-OUT mix color hotend, it has three input channels and one nozzle. Three filaments are mixed in the mixing chamber in the heating block and extruded through the nozzle.  
We have mass produced four versions of M3 hot end. For details, please refer to the documents in the "**M3 3-IN-1-OUT mixing color Hotend**" directory.  

### :file_folder: [M2P1 (3-IN-2-OUT Mix Color) Hotend](./M2P1/)
**M2P1** hot end is a 3-IN-2-OUT mix color hotend, it has three input channels and two nozzles. Two filaments are mixed in the heating block and extruded through one of the nozzle, another independent nozzle can be used to print the support filament.   
Simply put, it is a combination of an M2 hot end and a single color hot end. It has the advantages of M2, singel nozzle hot end and double nozzle hot end. It can meet the needs of printing singel color, mixed color and two-color, as well as singel color+ support (such as PLA + PVA).

### :file_folder: [R3 (3-IN-3-OUT Non-Mix color) Hotend](./R3/)
**R3** hot end is a 3-IN-3-OUT non-mix color hotend, it has three input channels and three nozzles, and all of the three nozzle share one heater and temperature sensor.  
For details, please refer to [**here**](./R3/readme.md).  

------
## 2 Channels Hotend
### :file_folder: [M2 (2-IN-1-OUT Mix color) Hotend](./M2/)
**M2** hot end is a 2-IN-1-OUT mix color hotend, it has two input channels and one nozzle. Two filaments are mixed in the heating block and extruded through the nozzle.   
For details, please refer to [**here**](./M2/readme.md).  

### :file_folder: [R2 (2-IN-2-OUT Non-Mix color) Hotend](./R2/)
**R2** hot end is a 2-IN-2-OUT hotend, it has two input channels and 2 nozzles. Two filaments can be loaded into the heating block and extruded through the nozzle.   
**R2S** is similar to **R2** hot end, but the two nozzles of R2S share the same heater and temperature sensor, so the temperatures of the two channels of R2S hot end cannot be set separately.     
For details, please refer to [**here**](./R2/). 

------
## One Color Hotend
- **[:book: Instructions for Single color Hotend](./Single_color/readme.md).**
- **[:book: Instructions for High Flow Single color Hotend](https://github.com/ZONESTAR3D/Upgrade-kit-guide/tree/main/HOTEND/Single_color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).**

<!-- ------
## :file_folder: [Slicing Guide for ZONESTAR 3D Printer](https://github.com/ZONESTAR3D/Slicing-Guide)
[:book:Details](https://github.com/ZONESTAR3D/Slicing-Guide) -->

------
## :gift: How to buy
- **One color Hotend**   
  - **General Flowrate one color hotend** [**:gift: Buy (Aliexpress)**](https://www.aliexpress.com/item/1005001275334841.html)
  - **High Flowrate one color hotend** [**:gift: Buy (Official Store)**](https://bit.ly/3RF7ciR) [**:gift: Buy (Aliexpress)**](https://www.aliexpress.com/item/1005001275334841.html)
- **2 Channels Hotend (2-IN-1-OUT/2-IN-2-OUT)**
[**:gift: Buy (Aliexpress)**](https://www.aliexpress.com/item/1005001285955926.html)
- **3 Channels Hotend (3-IN-1-OUT/3-IN-2-OUT/3-IN-3-OUT)** [**:gift: Buy (Official Store)**](https://bit.ly/3z37ZUo)   [**:gift: Buy (Aliexpress)**](https://www.aliexpress.com/item/1005001275429959.html) 
- **4 Channels Hotend (M4 Hotend and E4 Hotend)**
  - **E4 (4-IN-1-OUT Non-mix Color) Hotend**
  [**:gift: Buy (Official Store)**](https://bit.ly/39qDtKp) [**:gift: Buy (Aliexpress)**](https://www.aliexpress.com/item/1005002951777699.html)
  - **M4V6 Hotend**
  [**:gift: Buy (Official Store)**](https://bit.ly/3QhWJtf)  [**:gift: Buy (Aliexpress)**](https://www.aliexpress.com/item/1005004547646195.html)
  - **M4V4 & M4V5 (Older Version 4-IN-1-OUTmix Color) Hotend**
  [**:gift: Buy (Aliexpress)**](https://www.aliexpress.com/item/1005001581641783.html)

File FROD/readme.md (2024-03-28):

### :globe_with_meridians: Choose Language (Translated by google)
(https://github-com.translate.goog/ZONESTAR3D/Upgrade-kit-guide?_x_tr_sl=en&_x_tr_tl=es)
(https://github-com.translate.goog/ZONESTAR3D/Upgrade-kit-guide?_x_tr_sl=en&_x_tr_tl=pt)
(https://github-com.translate.goog/ZONESTAR3D/Upgrade-kit-guide?_x_tr_sl=en&_x_tr_tl=fr)
(https://github-com.translate.goog/ZONESTAR3D/Upgrade-kit-guide?_x_tr_sl=en&_x_tr_tl=de)
(https://github-com.translate.goog/ZONESTAR3D/Upgrade-kit-guide?_x_tr_sl=en&_x_tr_tl=it)
(https://github-com.translate.goog/ZONESTAR3D/Upgrade-kit-guide?_x_tr_sl=en&_x_tr_tl=sv)
(https://github-com.translate.goog/ZONESTAR3D/Upgrade-kit-guide?_x_tr_sl=en&_x_tr_tl=pl)
(https://github-com.translate.goog/ZONESTAR3D/Upgrade-kit-guide?_x_tr_sl=en&_x_tr_tl=da)
(https://github-com.translate.goog/ZONESTAR3D/Upgrade-kit-guide?_x_tr_sl=en&_x_tr_tl=cs)
(https://github-com.translate.goog/ZONESTAR3D/Upgrade-kit-guide?_x_tr_sl=en&_x_tr_tl=hr)
(https://github-com.translate.goog/ZONESTAR3D/Upgrade-kit-guide?_x_tr_sl=en&_x_tr_tl=ro)
(https://github-com.translate.goog/ZONESTAR3D/Upgrade-kit-guide?_x_tr_sl=en&_x_tr_tl=sk)

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

-----
## Filament Run Out Sensor User Guide
:warning: **NOTE: In the following document, we will use FROD to represent "Filament Run Out Sensor"**.
### 1. Introduction of FROD
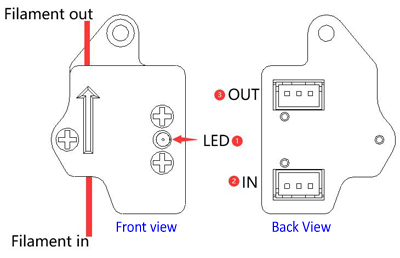
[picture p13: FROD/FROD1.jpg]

- **LED:** Filament detection indicator light, it will light up when the filament is inserted.
- **"IN" Connector:** Connect to  the control board or the previous FROD.
- **"OUT" Connector:** Connect to the next FROD. Let it suspend if there is not the next one.   
:bulb:  The filament must be inserted in the direction indicated by the arrow.     

### 2. Wiring
#### Wiring Diagram of FROD
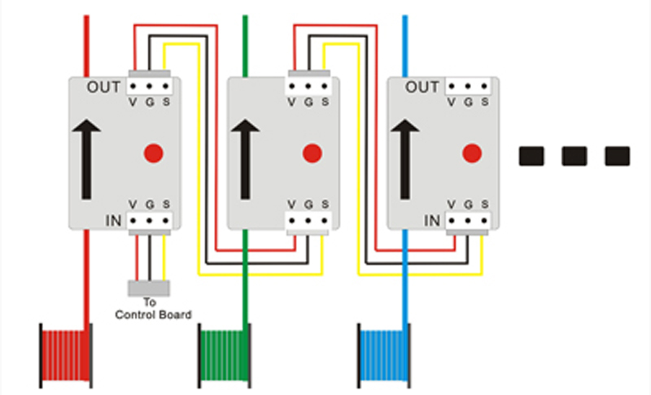
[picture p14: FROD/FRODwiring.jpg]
    
:warning: **Please pay attention to distinguishing between IN and OUT connectors of the FROD, as incorrect connections may cause the machine to fail to start up or even burn the control board.**    
:warning: **The "Filament Run Out Sensors" (there are 4 pieces for Z9V5Pro / Z8PM4Pro) were series connected, if any one "filament run out" was detected, the printer will pause printing.**    

#### Wiring FROD to the machine
Connect the FROD to the corresponding port on the motherboard of the machine. For the motherboard port allocation diagram (wiring diagram), please refer to the installation and wiring manual of the machine. **:point_right:[Z8P Wiring Diagram](https://github.com/ZONESTAR3D/Z8P/blob/main/Z8P-MK2/1-Installation_Guide/Z8PM4-MK2_Wiring_Diagram.jpg)**. **:point_right:[Z9V5 Wiring Diagram](https://github.com/ZONESTAR3D/Z9/blob/main/Z9V5/Z9V5-MK4/1.Installation_and_User_Guide/Wiring/Z9V5Pro_Wiring_Diagram.jpg)**.    

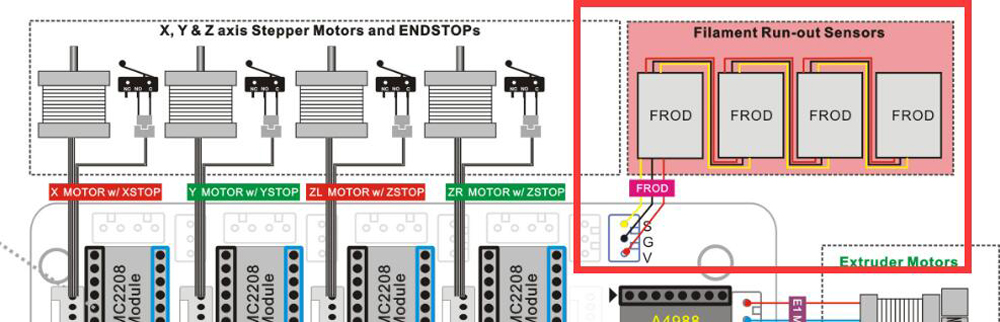
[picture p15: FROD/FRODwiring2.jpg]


### 3. User Guide of FROD
:bulb: ***This document takes Z9V5Pro as an example.***    
[:clapper: Video tutorial(for Z9V5Pro)](https://youtu.be/QCJ-6L6ze1w)    
If there is not enough filaments left in the filament roll to complete the current printing, you can enable the ***"Runout Sensor"*** feature. The machine will pause the printing when detected the filament is run out, then you can load a new filament roll and resume the printing. What you need to do is:    
1. Pass the filament through the FROD.
2. Turn on the **run out** feature on LCD screen.      
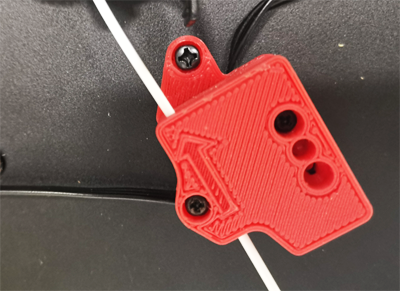
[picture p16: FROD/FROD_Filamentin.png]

### :warning: Notice
1. The printing pause may cause some obvious defects on the prints.    
2. If the filament was enough when printing the current gcode file, bypassed the filament from the FROD and load it into the extruders directly, and turn off the **run out** feature on LCD screen.         
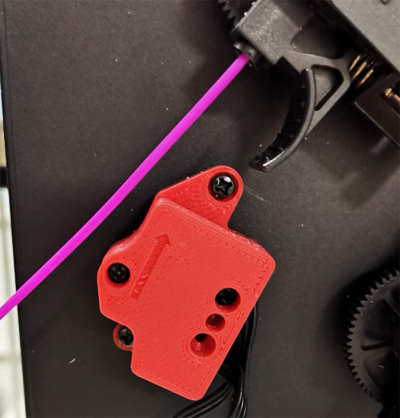
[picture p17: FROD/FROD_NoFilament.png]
      
3. If you need to use the Filament run out detect function, you should insert filaments on all 4 sensors. If you do not actually use 4 filaments when printing, please cut a little filament and insert it into the FROD of the unused extruders.   
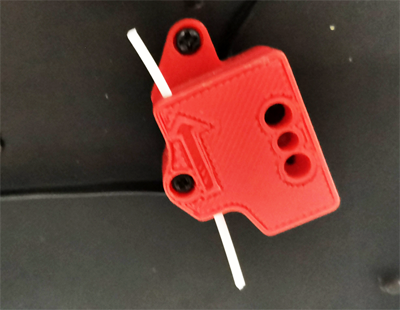
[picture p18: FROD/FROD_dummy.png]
     

### 4. Installation guide
- **[:clapper: Install filament run out sensor on Z8P 3D Printer](https://youtu.be/mLexZ0az_Ps)**

-----
## Case Stl File of FROD
- **FRODV6-new (for Z9V5-MK6 or Z9V5Pro upgrade Dual Gear Extruders) [:arrow_down: Download stl file](./FRODV6B.zip)**     
After Z9V5 upgraded to the Dual Gear Extruder, the position of the feed inlet of the new extruder was different from the original extruder, so the FRODV6 needed to be adjusted. We modified the bottom cover of the FRODV6 case.    
PS: The left and right extruders used different bottom covers.    
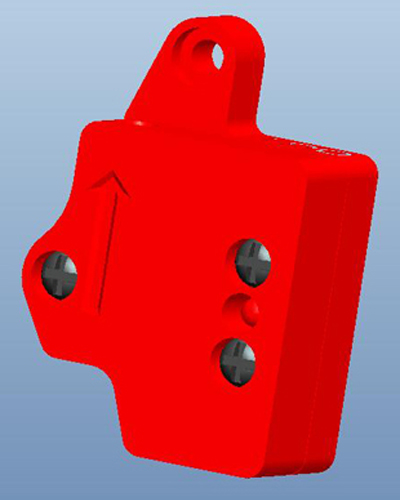
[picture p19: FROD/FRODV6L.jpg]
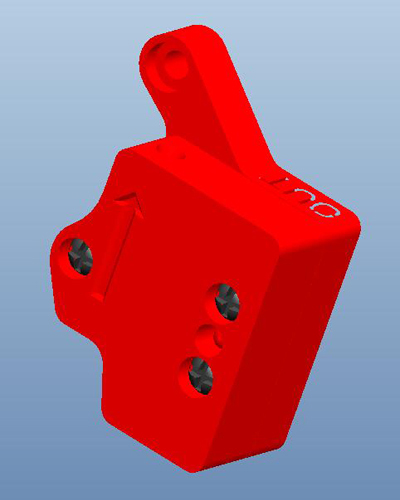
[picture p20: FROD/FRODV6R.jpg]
        

- **FRODV6 (for Z9V5-MK1/2/3/4/5 and Z8P) [:arrow_down: Download stl file](./FRODV6.zip)**    
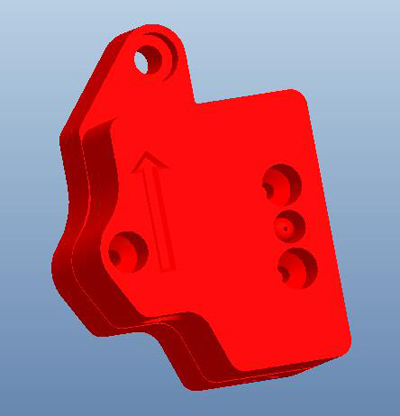
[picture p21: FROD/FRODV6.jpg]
    

- **FRODV4 (for P802, Z5, Z5X, Z6, Z8T, Z9M2, Z9M3, Z9M4) [:arrow_down: Download stl file](./frodv4.zip)**   
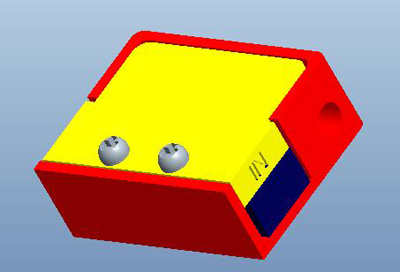
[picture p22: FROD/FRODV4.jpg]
    

----
### Bracket for Z9M3/Z9M4 [:arrow_down: Download stl file](./z9_frod_br.zip)
The stl file of a bracket the FROD to the extruder motors of the Z9M3 and Z9M4 3d printer kit.    
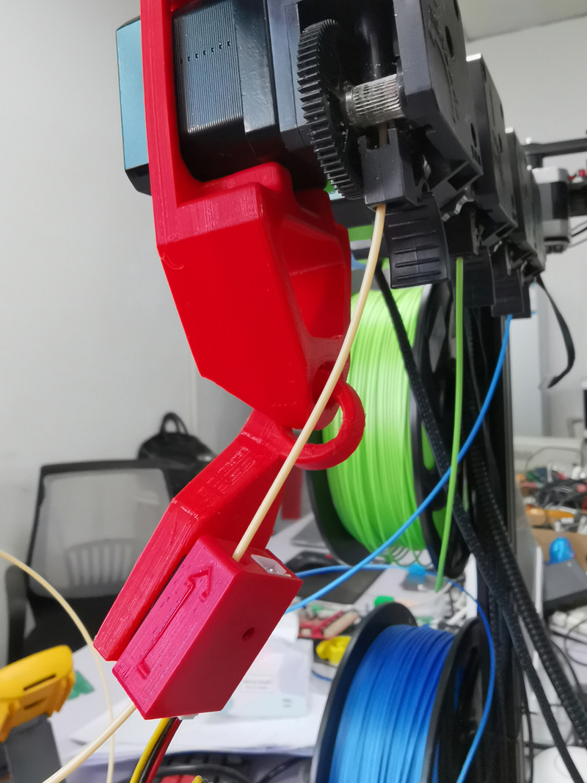
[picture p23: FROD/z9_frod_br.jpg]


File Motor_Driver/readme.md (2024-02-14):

## :warning: ATTENTION PLEASE
- **Power off the control board before replacing/plugin the drive module.**
- **Pay attention to the direction when plugin, incorrect direction may burn the drivers and control board.**
- **Usually we have already set the motor drive current before shipping out, please don't tune the potentiometer if you are not sure how to adjust it.**
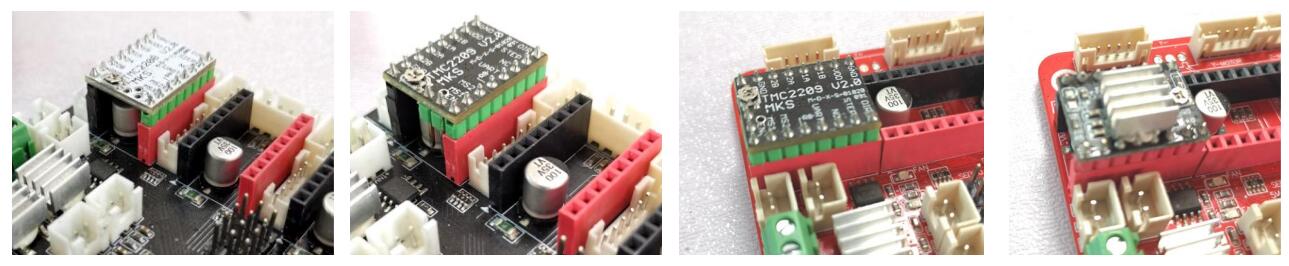
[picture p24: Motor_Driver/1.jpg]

### How to change working direction by exchange motor wiring 
You may need to change the stepper motor working direction after replaced the motor drivers, such as replaced A4988 to TMC2208, you can upgrade the appropriate firmware to the control board or adjust the motor wiring to reserved the motor working direction.
- Simply exchange PIN1 and PIN3 of the motor cable, the stepping motor working direction will be reversed.

- TIPS: Use a knife to turn up the clip of the terminal and then pull out the wiring


### How to adjust drive current
If you want to adjust the current of the motor driver module, please measure the voltage (Vref) on the potentiometer with a multimeter.     
**:loudspeaker: NOTE**
- **Diconnected the motor wire and then supply power to the control board.**
- **For A4988 drive module, you can supply power to the control board from USB, but for TMC drive module, it must supply power to the control board from DC terminal.**


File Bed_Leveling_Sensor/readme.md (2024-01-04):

### :globe_with_meridians: Choose Language (Translated by google)
(https://github-com.translate.goog/ZONESTAR3D/Upgrade-kit-guide?_x_tr_sl=en&_x_tr_tl=es)
(https://github-com.translate.goog/ZONESTAR3D/Upgrade-kit-guide?_x_tr_sl=en&_x_tr_tl=pt)
(https://github-com.translate.goog/ZONESTAR3D/Upgrade-kit-guide?_x_tr_sl=en&_x_tr_tl=fr)
(https://github-com.translate.goog/ZONESTAR3D/Upgrade-kit-guide?_x_tr_sl=en&_x_tr_tl=de)
(https://github-com.translate.goog/ZONESTAR3D/Upgrade-kit-guide?_x_tr_sl=en&_x_tr_tl=it)
(https://github-com.translate.goog/ZONESTAR3D/Upgrade-kit-guide?_x_tr_sl=en&_x_tr_tl=sv)
(https://github-com.translate.goog/ZONESTAR3D/Upgrade-kit-guide?_x_tr_sl=en&_x_tr_tl=pl)
(https://github-com.translate.goog/ZONESTAR3D/Upgrade-kit-guide?_x_tr_sl=en&_x_tr_tl=da)
(https://github-com.translate.goog/ZONESTAR3D/Upgrade-kit-guide?_x_tr_sl=en&_x_tr_tl=cs)
(https://github-com.translate.goog/ZONESTAR3D/Upgrade-kit-guide?_x_tr_sl=en&_x_tr_tl=hr)
(https://github-com.translate.goog/ZONESTAR3D/Upgrade-kit-guide?_x_tr_sl=en&_x_tr_tl=ro)
(https://github-com.translate.goog/ZONESTAR3D/Upgrade-kit-guide?_x_tr_sl=en&_x_tr_tl=sk)

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

## :file_folder:[PL-08N](./PL-08N/) 
**PL-08N** is a proximity sensor, it can probing metal hotbed. If your hot bed surface is metal, such as aluminum plate + hot bed adhesive tape, aluminum plate + magnetic hot bed paste, elastic rigid hot bed, etc., you can use this sensor.       
[:gift:**Sell Link**](https://www.aliexpress.com/item/4000596309710.html)  
### User guide of PL-08N
- **[:book: User guide for LCD128x64 screen](./PL-08N/ABL_LCD12864.md)**
- **[:book: User guide for DWIN_LCD screen](./PL-08N/ABL_LCDDWIN.md)**

## :file_folder:[ZL-Sensor](./ZL-Sensor/) 
**ZL-Sensor** is a special photoelectric sensor made by ZONESTAR, it can probing almost all meterial hotbed, also it is easier to wiring such as PL-08N. The use of ZL Sensor is the same as PL-08N. Please refer to the [**user guide for PL-08N**](#user-guide-of-pl-08n).    
[:gift:**Sell Link**](https://www.aliexpress.com/item/1005002865311470.html)  

## :file_folder:[3DTouch](./3DTouch/)
**BLtouch(3DTouch)** is a "famous" bed auto leveling sensor for 3D Printers, it integrates a simple servo motor and an electromagnetic sensor into a very small volume. It can be used for all types of heat beds with high accuracy. The disadvantage is that the wiring and use are a little complex.    
**:book: [User guide](./3DTouch/How%20to%20Upgrade%20Bed%20Auto%20Leveling%20Feature(BL-Touch)%20V5.pdf)**     
[:gift:**Sell Link**](https://www.aliexpress.com/item/1005001464420529.html)

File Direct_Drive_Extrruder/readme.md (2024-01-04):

### :globe_with_meridians: Choose Language (Translated by google)
(https://github-com.translate.goog/ZONESTAR3D/Upgrade-kit-guide?_x_tr_sl=en&_x_tr_tl=es)
(https://github-com.translate.goog/ZONESTAR3D/Upgrade-kit-guide?_x_tr_sl=en&_x_tr_tl=pt)
(https://github-com.translate.goog/ZONESTAR3D/Upgrade-kit-guide?_x_tr_sl=en&_x_tr_tl=fr)
(https://github-com.translate.goog/ZONESTAR3D/Upgrade-kit-guide?_x_tr_sl=en&_x_tr_tl=de)
(https://github-com.translate.goog/ZONESTAR3D/Upgrade-kit-guide?_x_tr_sl=en&_x_tr_tl=it)
(https://github-com.translate.goog/ZONESTAR3D/Upgrade-kit-guide?_x_tr_sl=en&_x_tr_tl=sv)
(https://github-com.translate.goog/ZONESTAR3D/Upgrade-kit-guide?_x_tr_sl=en&_x_tr_tl=pl)
(https://github-com.translate.goog/ZONESTAR3D/Upgrade-kit-guide?_x_tr_sl=en&_x_tr_tl=da)
(https://github-com.translate.goog/ZONESTAR3D/Upgrade-kit-guide?_x_tr_sl=en&_x_tr_tl=cs)
(https://github-com.translate.goog/ZONESTAR3D/Upgrade-kit-guide?_x_tr_sl=en&_x_tr_tl=hr)
(https://github-com.translate.goog/ZONESTAR3D/Upgrade-kit-guide?_x_tr_sl=en&_x_tr_tl=ro)
(https://github-com.translate.goog/ZONESTAR3D/Upgrade-kit-guide?_x_tr_sl=en&_x_tr_tl=sk)

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

-----
## Direct Driver Extrude Installation, Wiring and Setup Guide
### 1. Installation
#### :movie_camera:[**Video tutorial**](https://youtu.be/_s9Yc3zy6vw) 
Note: This video tutorial is based on upgrading DDE from Z9V5Pro.
#### Installation steps
+ **Step 1**. Take down the orignal hotend from the x carrier.  
+ **Step 2**. Install the direct drive extruder (DDE ) to the same position of the carrier.  
DDE_Installation
### 2. Wiring
Wiring
**if the stepper motor working direction is reserved, you can change change the stepping motor direction by modified the wire**  
DDE_Installation  
### 3. Set the steps/mm parameter
**You may need to change the steps/mm parameter of the extruder, there are two method to set the steps/mm parameter**  


-----

-----
## Appendix
### Appendix 1: How to install bed leveling sensor

### Appendix 2: How to fix HOME X issue for Z9V5-MK1 and Z9V5-MK2

### Appendix 3: How to open the control box of Z9V5Pro
Loosen the four screws to open the upper control box and then you can find the wire for extrude motors, connect the wire to E1 motor connecotor.  

### Appendix 4: Print parts of DDE
- **[:book: About the print parts](./stl/readme.md)**  
- **[:arrow_down: Download print parts stl file](./stl/stl.zip)**
### Appendix 5: Correct X&Y offset
The hot bed center moves after replacing the extruder, you can set it on LCD screen if you care about it, please upload the newest firmware to your printer. About how to set the home offset, please refer to [:arrow_right:this guide](https://github.com/ZONESTAR3D/Document-and-User-Guide/blob/master/common/set_offset.md).   
Firmware Download link:    
- [**Z9V5**](https://github.com/ZONESTAR3D/Firmware/tree/master/Z9/Z9V5/bin)  
- [**Z8P**](https://github.com/ZONESTAR3D/Firmware/tree/master/Z8/Z8P/ZM3E4)

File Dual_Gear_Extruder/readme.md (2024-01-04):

### :globe_with_meridians: Choose Language (Translated by google)
(https://github-com.translate.goog/ZONESTAR3D/Upgrade-kit-guide?_x_tr_sl=en&_x_tr_tl=es)
(https://github-com.translate.goog/ZONESTAR3D/Upgrade-kit-guide?_x_tr_sl=en&_x_tr_tl=pt)
(https://github-com.translate.goog/ZONESTAR3D/Upgrade-kit-guide?_x_tr_sl=en&_x_tr_tl=fr)
(https://github-com.translate.goog/ZONESTAR3D/Upgrade-kit-guide?_x_tr_sl=en&_x_tr_tl=de)
(https://github-com.translate.goog/ZONESTAR3D/Upgrade-kit-guide?_x_tr_sl=en&_x_tr_tl=it)
(https://github-com.translate.goog/ZONESTAR3D/Upgrade-kit-guide?_x_tr_sl=en&_x_tr_tl=sv)
(https://github-com.translate.goog/ZONESTAR3D/Upgrade-kit-guide?_x_tr_sl=en&_x_tr_tl=pl)
(https://github-com.translate.goog/ZONESTAR3D/Upgrade-kit-guide?_x_tr_sl=en&_x_tr_tl=da)
(https://github-com.translate.goog/ZONESTAR3D/Upgrade-kit-guide?_x_tr_sl=en&_x_tr_tl=cs)
(https://github-com.translate.goog/ZONESTAR3D/Upgrade-kit-guide?_x_tr_sl=en&_x_tr_tl=hr)
(https://github-com.translate.goog/ZONESTAR3D/Upgrade-kit-guide?_x_tr_sl=en&_x_tr_tl=ro)
(https://github-com.translate.goog/ZONESTAR3D/Upgrade-kit-guide?_x_tr_sl=en&_x_tr_tl=sk)

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

-----
# Dual Gear Extruder
### BMG Extruder
The BMG utilizes an internal gearing ratio of 3:1 together with precision CNC-machined hardened steel drive gears to give you a compact powerhouse for all your applications.
Whether you require high resolution prints with small nozzles or high-flow prints with big nozzles the optimized gearing ratio combined with our industry leading drive gears provides unparalleled pushing power and lightning fast retractions in a lightweight and compact package.
The extruder is sold without motor.
BMG is available in both left hand and right hand. 

### Technical Specification
- **Net weight:** 75g
- **Gross weight:** 139g
- **Package dimension:** 137×94×65mm
- **Gearing ratio:** 3:1
- **Filament diameter:** 1.75mm, Capable of supporting 2.85mm after simple modifications
- **Operating temperature:** 0–80°C

### Dimensions


### More information about BMG Extruder
- **[:clapper:Install BMG Extruder ](https://youtu.be/87OYybHhPFA)**
- **[:clapper:How a BMG extruder works and why it's so good](https://youtu.be/f2KTWnF3r1k)**

-----
# Manual for Upgraded Dual Gear Extruder 
## [:book: P802Q Upgraded Dual Gear Extruder Manual](./P802Q.md)
## [:book: Z9V5Pro Upgraded Dual Gear Extruder Manual](./Z9V5.md)
## [:book: Z8P Upgraded Dual Gear Extruder Manual](./Z8P.md)

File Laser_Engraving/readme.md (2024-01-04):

### :globe_with_meridians: Choose Language (Translated by google)
(https://github-com.translate.goog/ZONESTAR3D/Upgrade-kit-guide?_x_tr_sl=en&_x_tr_tl=es)
(https://github-com.translate.goog/ZONESTAR3D/Upgrade-kit-guide?_x_tr_sl=en&_x_tr_tl=pt)
(https://github-com.translate.goog/ZONESTAR3D/Upgrade-kit-guide?_x_tr_sl=en&_x_tr_tl=fr)
(https://github-com.translate.goog/ZONESTAR3D/Upgrade-kit-guide?_x_tr_sl=en&_x_tr_tl=de)
(https://github-com.translate.goog/ZONESTAR3D/Upgrade-kit-guide?_x_tr_sl=en&_x_tr_tl=it)
(https://github-com.translate.goog/ZONESTAR3D/Upgrade-kit-guide?_x_tr_sl=en&_x_tr_tl=sv)
(https://github-com.translate.goog/ZONESTAR3D/Upgrade-kit-guide?_x_tr_sl=en&_x_tr_tl=pl)
(https://github-com.translate.goog/ZONESTAR3D/Upgrade-kit-guide?_x_tr_sl=en&_x_tr_tl=da)
(https://github-com.translate.goog/ZONESTAR3D/Upgrade-kit-guide?_x_tr_sl=en&_x_tr_tl=cs)
(https://github-com.translate.goog/ZONESTAR3D/Upgrade-kit-guide?_x_tr_sl=en&_x_tr_tl=hr)
(https://github-com.translate.goog/ZONESTAR3D/Upgrade-kit-guide?_x_tr_sl=en&_x_tr_tl=ro)
(https://github-com.translate.goog/ZONESTAR3D/Upgrade-kit-guide?_x_tr_sl=en&_x_tr_tl=sk)

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

-----
# Laser Engine Installation and Engraving Operation Guide
## :warning: ATTENTION PLEASE
### :loudspeaker: DONOT turn on the power of the 3D printer and laser engine before installing the laser and completing the wiring, 
### :loudspeaker: DONOT turn on the laser power without wearing glasses.
### :loudspeaker: DONOT use the laser without personnel monitoring.
### :loudspeaker: DONOT use the laser without a fire extinguisher nearby.
### :loudspeaker: It is recommended to equipe an exhaust fan because it may generate smoke and dust when engraving.

-----
## [Installation & Wiring](./Installation/readme.md)

- :book: Refer to [**this guide**](./Installation/readme.md) to install the laser engine to the printer.
  - :arrow_down:[**Click here**](./Installation/lkbr_V2.zip) to download the bracket stl and gcode file if need.
- :book: Connect the laser engine wire to the control board and laser engine.

-----
## Prepare

### :one: Protect the hot bed
Put a wood board (thickness >= 5mm) or a ceramic tile to the bed to prevent it from being damaged by laser light. 
- For Z9V5Pro, you can remove the hotbed and put a (300mmx300mm) wood board to the bracket of the hot bed.

- For Z8, you can put a (300mmx300mm) wood board to the bracket of the hot bed.

### :two: Turn on the laser engine feature
:warning: If you can't find this MENU on your LCD screen, please upgrade the firmware of your 3d printer.
1. Turn on 3d printer.
2. Turn on "laser" setting on LCD MENU. "Control>>Configre>>Laser".
### :three: Adjust the focal of the laser engine
Follow the steps below to adjust the focal length of the laser, to operate using the LCD menu:   
1. Set the fan speed to 0. ***Prepare>>Temperature>>Fan: 0***
2. Home the laser enging head. ***Prepare>>Auto Home>>Home All***
3. Move the Z axis to 50mm. ***Prepare>>Move>>Move Z: 50***
4. Move the laser engine above the carved object. ***Prepare>>Move>>Move X & Prepare>>Move>>Move Y***
5. Turn on the power supply of the laser engine.
6. Increase the fan speed slowly until you can see the laser light spot clearly. ***Prepare>>Temperaure>>Fan: xx***
7. Rotate the lens knob of the laser engine to adjust the laser light spot size to the minimum.
8. Set the fan speed to 0, and then turn off the laser power supply. ***Prepare>>Temperature>>Fan: 0***

-----
## Operation Guide
You can use LaserWeb or inkscape to genarate the gcode file and then doing engrave. 
### :+1: [:book:LaserWeb Use Guide](./LaserWeb/readme.md)
### [:book:inkscape Use Guide](./inkscape/readme.md)

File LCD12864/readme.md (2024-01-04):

### :globe_with_meridians: Choose Language (Translated by google)
(https://github-com.translate.goog/ZONESTAR3D/Upgrade-kit-guide?_x_tr_sl=en&_x_tr_tl=es)
(https://github-com.translate.goog/ZONESTAR3D/Upgrade-kit-guide?_x_tr_sl=en&_x_tr_tl=pt)
(https://github-com.translate.goog/ZONESTAR3D/Upgrade-kit-guide?_x_tr_sl=en&_x_tr_tl=fr)
(https://github-com.translate.goog/ZONESTAR3D/Upgrade-kit-guide?_x_tr_sl=en&_x_tr_tl=de)
(https://github-com.translate.goog/ZONESTAR3D/Upgrade-kit-guide?_x_tr_sl=en&_x_tr_tl=it)
(https://github-com.translate.goog/ZONESTAR3D/Upgrade-kit-guide?_x_tr_sl=en&_x_tr_tl=sv)
(https://github-com.translate.goog/ZONESTAR3D/Upgrade-kit-guide?_x_tr_sl=en&_x_tr_tl=pl)
(https://github-com.translate.goog/ZONESTAR3D/Upgrade-kit-guide?_x_tr_sl=en&_x_tr_tl=da)
(https://github-com.translate.goog/ZONESTAR3D/Upgrade-kit-guide?_x_tr_sl=en&_x_tr_tl=cs)
(https://github-com.translate.goog/ZONESTAR3D/Upgrade-kit-guide?_x_tr_sl=en&_x_tr_tl=hr)
(https://github-com.translate.goog/ZONESTAR3D/Upgrade-kit-guide?_x_tr_sl=en&_x_tr_tl=ro)
(https://github-com.translate.goog/ZONESTAR3D/Upgrade-kit-guide?_x_tr_sl=en&_x_tr_tl=sk)

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

-----
## LCD12864 (OLED12864) Menu Description
   

### Function of knob
- **Clockwise rotation**: Menu item + / Value +
- **Counterclockwise rotation**: Menu item - / Value -
- **Push (click)**: Open Menu / Enter

### Menu Desciption
#### 1. status menu

| No. | Description | No. | Description | No. | Description | No. | Description |
|-----|---|-----|---|-----|---|-----|---|
|  1  |Current hotend temperature|  2  |Setting hotend temperature|  3  |Current hotbed temperature|  4  |Setting hotbed temperature|
|  5  |Current X/Y/Z position |  6  |Extrude fan speed |  7  |Multiple of print speed |  8  |SD card print progress |
|  9  |Status message |  10 |mix rate of extruders |  11 |Current VTool / Mix Mode  | | |

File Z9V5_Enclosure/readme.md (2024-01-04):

### :globe_with_meridians: Choose Language (Translated by google)
(https://github-com.translate.goog/ZONESTAR3D/Upgrade-kit-guide?_x_tr_sl=en&_x_tr_tl=es)
(https://github-com.translate.goog/ZONESTAR3D/Upgrade-kit-guide?_x_tr_sl=en&_x_tr_tl=pt)
(https://github-com.translate.goog/ZONESTAR3D/Upgrade-kit-guide?_x_tr_sl=en&_x_tr_tl=fr)
(https://github-com.translate.goog/ZONESTAR3D/Upgrade-kit-guide?_x_tr_sl=en&_x_tr_tl=de)
(https://github-com.translate.goog/ZONESTAR3D/Upgrade-kit-guide?_x_tr_sl=en&_x_tr_tl=it)
(https://github-com.translate.goog/ZONESTAR3D/Upgrade-kit-guide?_x_tr_sl=en&_x_tr_tl=sv)
(https://github-com.translate.goog/ZONESTAR3D/Upgrade-kit-guide?_x_tr_sl=en&_x_tr_tl=pl)
(https://github-com.translate.goog/ZONESTAR3D/Upgrade-kit-guide?_x_tr_sl=en&_x_tr_tl=da)
(https://github-com.translate.goog/ZONESTAR3D/Upgrade-kit-guide?_x_tr_sl=en&_x_tr_tl=cs)
(https://github-com.translate.goog/ZONESTAR3D/Upgrade-kit-guide?_x_tr_sl=en&_x_tr_tl=hr)
(https://github-com.translate.goog/ZONESTAR3D/Upgrade-kit-guide?_x_tr_sl=en&_x_tr_tl=ro)
(https://github-com.translate.goog/ZONESTAR3D/Upgrade-kit-guide?_x_tr_sl=en&_x_tr_tl=sk)

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

-----
## Z9V5 Enclosure Assembly Guide

### Parts List

1. Cloth cover 
2. Rubber Magnetic Stripe  
3. Skeleton Connector 
4. Cable Tie 
5. PC plate  
6. Fibre rods

### Assembly Steps
1. Remove the top frame of Z9V5Pro and insert the "PC plate" into the groove of the profile on side of the control assembly, and then install the top frame back.



2. Assemble the skeleton according to the below picture and fix it on the front/rear profile of the top frame.



3. Turn the cloth cover over, insert two 4mm diameter fiber rods into the cloth grooves on both sides of the top of the cloth sleeve until they protrude from the small holes on the top. Then, insert the ends of the two protruding fiber rods into the metal connectors to connect them. Do it at the other side by the same steps.


4. Turn the cloth cover over, flatten the top so that the two fiber rods extend the same length as before. Then insert the top of the fiber rod into the connectors fixed to the top frame of the machine.


5. Fix the cloth cover on the frame of machine by the cable ties.



6. Pasted the rubber magnetic stripe on the front Z profiles.



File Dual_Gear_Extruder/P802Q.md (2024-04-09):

## Upgraded Dual Gear Extruder for P802Q 

### Step :one:: Print a bracket and install the Dual Gear Extruder
#### [:arrow_down:Download the stl file of bracket- left](./P802Q/BMG_BR_L.zip)




#### [:arrow_down:Download the stl file of bracket - right](./P802Q/BMG_BR_R.zip)





### Step :two:: Modify the motor wire to change the motor working direction
You may need to exchange the extruder stepping motor working direction after upgraded the dual gear extruder, you can simply modify the stepping motor wires to change it, for details, please refer to [:book:**this guide**](https://github.com/ZONESTAR3D/Upgrade-kit-guide/tree/main/Motor_Driver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).

### Step :three:: Change Esteps/mm parameters
Because the double gear extruder build in a reduction gear, you need to modify the steps/mm parameter of the control board. You can use the following methods to modify the steps/mm parameter:    
1. **[Only valid for Marlin firmware]** -If your machine is using the latest Marlin firmware, you can modify the E Steps/mm parameter on the LCD menu (***Configuration>>Advance Settings>>Steps/mm>>E Steps/mm:***), usually you can change the parameter to 400. Then execute (***Configuration>>Store Settings***) to save the parameters to the NVRAM on the control board.
2. **[Valid for both Marlin and Repeater firmware]** - You can also add a "M92 E400" command in the Start G-code of the slicing software to set the steps/mm parameter. If you need to save the parameters to the NVRAM of the control board, you need to add a "M500" command following the M92 command.

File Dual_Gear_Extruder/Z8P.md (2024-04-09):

## Upgraded Dual Gear Extruder for Z8P 
### Steps
1. Take down PTFE tubes from extruders.
2. Take down the orignal extruders from top profile of Z8P machine.
3. Replace the orignal titan extruders to dual gear extruders.
4. Refer to [the guide below](#how-to-change-motor-work-direction) to modify the motor wire if need.
### Video Tutorial
(https://www.youtube.com/watch?v=f5ftI0Afmhg)

----
### How to change motor work direction
If you used 4 right hand dual gear extruders, the extruder motor working direction will be reversed, please refer to the below steps to modify the motor wire.
- Simply exchange PIN1 and PIN3 of the motor cable, the stepping motor working direction will be reversed.

- TIPS: Use a knife to turn up the clip of the terminal and then pull out the wiring


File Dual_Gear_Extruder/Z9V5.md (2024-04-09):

## Upgraded Dual Gear Extruder for Z9V5 
<!-- ![](./Z9V5/Z9V5-MK6.jpg) -->
### Step :one: Replace  of the Titan Extruders by Dual Gear Extruders
1. Remove the upper box.
2. Replace the extruders to dual Gear Extruders.
3. Install the upper box back.
#### Video Tutorial
(https://www.youtube.com/watch?v=g0kHvk-SuuU)

### Step :two: Upload firmware to the control board
- If your printer model was Z9V5Pro-MK1/MK2, please download firmware from [:link: this link]().
- If your printer model was Z9V5Pro-MK3/MK4/MK5, please download firmware from [:link: this link (Z9V5ProMK4_BMGLR_Vxxx)](https://github.com/ZONESTAR3D/Firmware/tree/master/Z9/Z9V5/bin/Z9V5Pro-MK4/customized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).

### Step :three: Replace the case of the Filament run out sensor
You need to update the FROD base prints, please download the stl from above link, print it out and replace them. Filament run out sensor case download link: https://github.com/ZONESTAR3D/Z9/tree/main/Z9V5/Parts_Stl#filament-run-out-sensor .

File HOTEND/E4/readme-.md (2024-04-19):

[E4GUIDE]: https://github.com/ZONESTAR3D/Upgrade-kit-guide/blob/main/HOTEND/E4/User_guide/readme.md
[PRELOAD]: https://github.com/ZONESTAR3D/Upgrade-kit-guide/tree/main/HOTEND/E4/User_guide#7-pre-load-filaments
[E4WORKINGPRINCIPLE]:https://github.com/ZONESTAR3D/Upgrade-kit-guide/blob/main/HOTEND/E4/User_guide/readme.md#5-working-principle

----
## <a id="choose-language">:globe_with_meridians: Choose language </a>









<!-- [![](../../lanpic/SA.png)](https://github.com/ZONESTAR3D/Upgrade-kit-guide/tree/main/HOTEND/E4/readme-ar.md) -->

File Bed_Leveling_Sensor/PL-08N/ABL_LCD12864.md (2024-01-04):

## Bed Auto Leveling Feature Use and Debug Guide for PL-08N bed leveling sensor
### Wiring
1. Connect the PL-08N to the Z+(ZRIBV6) or Z1+(ZM3E4) connector on the control board.   
2. Power on the 3d printer (or control board).
3. The LED of PL-08N should light up When it is closed to the hot bed, the LED should turn off when it is far away from the hotbed.


### Install
1. Move HOTEND to the middle of hot bed and adjust height of HOTEND or print platform, let the nozzle almost touched hot bed.   
2. Install the Proximity sensor on the HOTEND. The bottom of the sensor should be approximately 2-4 mm above the nozzle.
   
:warning: The sensing distance of PL-08N to aluminum plate is about 3 ~ 5mm, and to stainless steel is 5 ~ 8mm. If you use a PEI stainless steel hot bed film, please raise the installation position to 4 ~ 6mm from the bottom of the nozzle.

---- 
### Level Corners
**[:clapper: Auto Home](./video/AutoHome.gif)**    
**[:clapper: Level Corners](./video/Level_conrers.gif)**   
:loudspeaker: The automatic bed leveling function is used to correct the relative offset of different positions on the hot bed at the Z-axis height, not the absolute value. Before executing Bed Auto Leveling, you must perform **Level Corners** to make the machine obtain a correct absolute value of the starting point of Z axis (it is so called **Z axis absolute zero point** of the machine). Steps as below:    
1. Make sure the hotbed and nozzle are cool, clean the filament on the nozzle.
2. Turn on the 3d printer.
3. See ***Montion>> Bed Leveling>> Bed Leveling: OFF***, if it is **ON**, set to **OFF**.
4. Do ***Montion>> Bed Leveling>> Auto HOME*** on LCD screen. 
5. Do ***Montion>> Bed Leveling>> Level Corners(Fig3)*** on LCD screen. 
6. Adjust the screws under the hotend, let the nozzle almost to touch the hot bed(Fig4).
7. Following the wizard shown on LCD screen to adjust all the screws in the 4 corners of bed.
8. Perform at least 2 cycles to confirm that the screws at the bottom of the hot bed have been adjusted.
      
  
### Catch Probe Z offset
**[:clapper: Catch Probe Z offset](./video/CatchOffset.gif)**    
**"Probe Z Offset"** indicates the distance from the nozzle to the hot bed when the sensor sensed the hot bed.      
If the sensor is installed correctly, the nozzle is always above the hot bed when the sensor sensed the hot bed, so **Probe Z Offset** is always a negative value. Because the sensing distance of each PL-08N sensor is different, and the actual installation height of PL-08N is also different, so the **Probe Z Offset** of each machine is different too.     
You need to do ***Catch Z offset*** to get the **Probe Z Offset** before doing bed auto leveling. Steps as below: 
1. Do ***Montion>> Bed Leveling>> Auto HOME(Fig1).***
2. Do ***Montion>> Bed Leveling>> Catch Z Offset(Fig2).***
3. Wait the catching done, and then check the Z Probe offset on menu ***Montion>> Bed Leveling>> Probe Z Offset(Fig3).***
     
:warning: The Probe Z offset value of your machine may be different from the above picture.      

### Level Bed
**[:clapper: Level Bed](./video/bed_level.gif)**    
After completing the above steps, we have a reliable sensor to measure the hotbed surface and already set all its parameters. Now we need the machine to make a comprehensive measurement of the surface of the hot bed, so as to get a data sheet of the hot bed height on the surface.   
Do the below steps: 
1. Do ***Montion>> Bed Leveling>> Auto HOME(Fig1)***
2. Do ***Montion>> Bed Leveling>> Level Bed(Fig2)***
3. Wait for the end of the measure(Fig3). 
4. Do ***Montion>> Bed Leveling>> Auto HOME(Fig1)*** the auto leveling will change from "off" to "on". It indicates that the automatic leveling feature is working(Fig4).
     

### Verification
**[:clapper: Verification](./video/Printing_test.gif)**       
Now you can try to print a test file to verfiy the bed auto leveling result. Steps as below:   
1. Copy **[level_test_310.gcode :arrow_down:](./level_test_310.zip)** to SD card and print it from SD card.
2. When printing started, double click (click twice in one second) the knob to open Probe Z offset menu (fig1).
3. Rotate the knob and watch the nozzle, let the nozzle is higher than the hotbed about 0.3mm (fig2).
4. Do on the MENU>>Configuration>>Store settings (fig3)
     

### Apply bed auto leveling
#### :one: Auto leveling feature will be disable automatically when the printer reset, you can turn it on manually:
1. Do **Motion>> Bed Leveling>> Level Bed >>Auto Home**
2. Do **Motion>> Bed Leveling>> Level Bed >>bed leveling: OFF Change to ON**
ATTENTION: After do these 2 steps, the printer will apply the hotbed auto leveling correction by using the stored parameters in the last time. 
#### :two: You can also add command to the "Start Gcode" of slicer, let the printer do bed auto leveling when printing from SD card.
You can also add a G29 command following the G28 commant to the “start gcode” of slicing software, it will execute "bed auto leveling" in the star of printing.   


### :warning: ATTENTION PLEASE
If the following conditions occur, the parameters of the hot bed leveling table may change, you need to repeat all steps starting from **level Corners** to get the bed auto leveling data again.     
1. Adjust the screws at the bottom of the hot bed.
2. The print head was reinstalled causing the nozzle height to change.
3. The installation position of the sensor has changed.
4. Replace a hotend sticker.
5. Reset the NVRAM of the control board.
6. Other.

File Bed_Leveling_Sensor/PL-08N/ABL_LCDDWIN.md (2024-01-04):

## Bed Auto Leveling Feature Use and Debug Guide for PL-08N bed leveling sensor
### Wiring
1. Connect the PL-08N to the Z+(ZRIBV6) or Z1+(ZM3E4) connector on the control board.   
2. Power on the 3d printer (or control board).
3. The LED of PL-08N should light up When it is closed to the hot bed, the LED should turn off when it is far away from the hotbed.


### Install
1. Move HOTEND to the middle of hot bed and adjust height of HOTEND or print platform, let the nozzle almost touched hot bed.   
2. Install the Proximity sensor on the HOTEND. The bottom of the sensor should be approximately 2-4 mm above the nozzle.
   
:warning: The sensing distance of PL-08N to aluminum plate is about 3 ~ 5mm, and to stainless steel is 5 ~ 8mm. If you use a PEI stainless steel hot bed film, please raise the installation position to 4 ~ 6mm from the bottom of the nozzle.

----
**[:clapper: Video Tutorial](https://youtu.be/R3RfGnxx8hY)**    
### Level Corners
:loudspeaker: The automatic bed leveling function is used to correct the relative offset of different positions on the hot bed at the Z-axis height, not the absolute value. Before executing Bed Auto Leveling, you must perform **Level Corners** to make the machine obtain a correct absolute value of the starting point of Z axis (it is so called **Z axis absolute zero point** of the machine). Steps as below:    
1. Make sure the hotbed and nozzle are cool, clean the filament on the nozzle.
2. Turn on the 3d printer.
3. Do ***Control>>Config>>Auto Leveling: OFF***, if it is **OFF**, set to **ONF**.     
    
4. Do ***Prepare>>Bed Leveling>>Auto Home*** on LCD screen. 
5. Do ***Prepare>>Bed Leveling>>Point1*** on LCD screen. 
6. Adjust the screws under the hotend, let the nozzle almost to touch the hotbed(Fig4).
7. Do ***Prepare>>Bed Leveling>>Point 2/3/4*** on LCD screen and Adjust the screws under the hotend, let the nozzle almost touched the hotbed.
8. Perform at least 2 cycles to confirm that the screws at the bottom of the hot bed have been adjusted.
    
After level coners, print ”level_test_310.gcode” from SD card, and check if the hotbed is enough level.      
    
Press the knob twice within one second to open the babysteps menu, and then rotate the knob to fine tune the distance from nozzle to hotbed.    
    

### Catch Probe Z offset
**"Probe Z Offset"** indicates the distance from the nozzle to the hot bed when the sensor sensed the hot bed.      
If the sensor is installed correctly, the nozzle is always above the hot bed when the sensor sensed the hot bed, so **Probe Z Offset** is always a negative value. Because the sensing distance of each PL-08N sensor is different, and the actual installation height of PL-08N is also different, so the **Probe Z Offset** of each machine is different too.     
You need to do ***Catch Z offset*** to get the **Probe Z Offset** before doing bed auto leveling. Steps as below: 
1. Do ***Prepare>> Bed Leveling>>Catch Z-Offset***
2. Wait the catching done, and then check the Z Probe offset on menu ***Montion>> Bed Leveling>> Probe Z Offset(Fig3).***
     
:warning: If "Catch Probe Z offset" fail, check if the probe installed too high.      
:warning: The Probe Z offset value of your machine may be different from the above picture.      

### Level Bed 
After completing the above steps, we have a reliable sensor to measure the hotbed surface and already set all its parameters. Now we need the machine to make a comprehensive measurement of the surface of the hot bed, so as to get a data sheet of the hot bed height on the surface.   
- Do ***Prepare>> Bed Leveling>>Auto Leveling***.
After measure done, the state of Auto leveling on Leveling menu will change from Unactived to Actived.
 
#### :warning: Note:   
1. The above image shows measuring 16 points total, but the number of measurement points may be different according to the machine varies.
2. The measurement result should be between -1.0 to 1.0 mm. If it exceeds, it is recommended that you try to fine tune the printer or improve the flatness of the hotbed, because it may affect the printing quality.
3. If it is found that there is a large deviation in data arrangement between the Left/Right sides or the Front/Back sides, please adjust the bottom screw of the hotbed (when the data is + turn down the hotbed, when the data is - turn up the hotbed)

### Verification     
Now you can try to print a test file to verfiy the bed auto leveling result. Steps as below:   
1. Copy level_test_310.gcode to SD card and print it from SD card.
2. When printing started, double click (click twice in one second) the knob to open baby Z offset menu.
3. Rotate the knob and watch the nozzle, let the nozzle is higher than the hotbed about 0.3mm.
     

### Apply bed auto leveling
#### :one: Auto leveling feature will be disable automatically when the printer reset, you can turn it on manually:
1. Do **Prepare>>Auto Home>>Home All**
2. Do **Prepare>>Bed Leveling>>Active Autolevel: OFF Change to ON**

ATTENTION: After do these 2 steps, the printer will apply the hotbed auto leveling correction by using the stored parameters in the last time. 
#### :two: You can also add command to the "Start Gcode" of slicer, let the printer do bed auto leveling when printing from SD card.
You can also add a G29 command following the G28 commant to the “start gcode” of slicing software, it will execute "bed auto leveling" in the star of printing.   


### :warning: ATTENTION PLEASE
If the following conditions occur, the parameters of the hot bed leveling table may change, you need to repeat all steps starting from **level Corners** to get the bed auto leveling data again.     
1. Adjust the screws at the bottom of the hot bed.
2. The print head was reinstalled causing the nozzle height to change.
3. The installation position of the sensor has changed.
4. Replace a hotend sticker.
5. Reset the NVRAM of the control board.
6. Other.

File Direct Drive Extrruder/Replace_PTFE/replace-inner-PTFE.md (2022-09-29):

## How to replace the inner PTFE tube of the direct drive extruder
- Loosen the screws to fix the FAN bracket.   


- Loosen the screws to fix the heater and temperature sensor, and remove the cartridge heater and temperature sensor from the aluminum heat block.    
  

- Take down the nozzle and the heating block from the throat.       
  

- Repleace a new PTFE tube (length is about 60mm).   
  

- Insert PTFE into the bottom, and cut the PTFE tube, let it extend from the throat about 1mm.
  

- Install the nozzle, heating block and then install the cartridge heater and temperature sensor to the aluminum heat block.   
You can put the wires of cartridge heater and temperature sensor on the outside and fastened with a tie. This makes it easy to install the cartridge heater.    


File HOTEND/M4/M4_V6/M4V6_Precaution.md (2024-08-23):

## <a id="choose-language">:globe_with_meridians: Choose language </a>











-----
##  <a id="en">Precautions for using M4V6</a>
### Cautions :bangbang: 
The M4V6 belongs to a ***Bowden extruder***. ***Bowden extruder*** refers to an extruder structure that separates **extruder** (filament feeder device) and the **"hot end"** (filament melting device). This structure can effectively reduce the weight of the print head, which is commonly used in multi-color 3D printers.  
     

    A. Filament           B. Extruder (filament feeder)       C. Feeding pipe   D. PTFE tube connector
    E. Inner PTFE tube    F. M4V6 Hotend                      G. Nozzle

#### :warning: Must connect the extruders with M4V6 hotend by using a pipes.
Must use pipes to connect the extruder to the connectors on the M4V6 hot end, so that the filaments can be pushed into the hot end.
The pipes require the use of harder materials and the interior should be very smooth. Currently, **PTFE tube** are commonly used. Don't use rubber or PVC tubes.


#### :warning: DON'T pull the "inner PTFE tubes" out of the M4V6 hotend.
The M4V6 hot end uses four white PTFE tubes inserted into the heating block of the hot end, which are called **"inner PTFE tubes"**, so that the filaments can be guided into the heating block for melting.
1. Do not pull **"inner PTFE tubes"** out of the M4V6 hotend , otherwise fine threads will enter the hot isolator and block the hot end.
2. Ensure that the **"inner PTFE tubes"** have been inserted into the bottom of the hot end, otherwise it may cause **hot end blocked issue** (much filament entering the heat insulation will block the hot end) or **"strings issue"** (a few filament melted in the heat insulation will reduce the effectiveness of the retraction).
3. It is not recommended to use colored PTFE pipes as **"inner PTFE tube"** because their temperature resistance performance is poor.    
##### :pushpin: If you would like to have a better understanding of the M4V6 hotend, please refer to the following image:
- [:art: Structure of M4V6 Hotend assembly](2.jpg)  
- [:art: Structure of M4V6 Hotend](1.jpg)


#### :warning: Must load 4 filaments onto the M4V6 hotend simultaneously.


-----
## <a id="es">Precauciones para usar M4V6</a> [:arrow_heading_up:](#choose-language)
### Precauciones :bangbang: 
El hot end M4V6 pertenece a una ***extrusora Bowden***. ***Extrusora Bowden*** se refiere a una estructura de extrusora que separa la **extrusora** (dispositivo alimentador de filamentos) y el **"extremo caliente"** (dispositivo de fusión de filamentos). Esta estructura puede reducir efectivamente el peso del cabezal de impresión, que se usa comúnmente en impresoras 3D multicolores.
     

    A. Filamento                B. Extrusor (alimentador de filamento)  C. Tubo de alimentación     D. Conector del tubo de PTFE
    E. Tubo interior de PTFE    F. Hotend M4V6                          G. Boquilla

#### :warning: Debe conectar los extrusores con el hotend M4V6 mediante tuberías.
Debe utilizar tuberías para conectar el extrusor a los conectores del extremo caliente M4V6, de modo que los filamentos puedan introducirse en el extremo caliente.
Las tuberías requieren el uso de materiales más duros y el interior debe ser muy liso. Actualmente, se utilizan comúnmente **tubos de PTFE**. No utilice tubos de goma o PVC.


#### :warning: NO saque los "tubos internos de PTFE" del hotend M4V6.
El hot end M4V6 utiliza 4 tubos de PTFE blancos insertados en el bloque calefactor del hot end, que se denominan **"tubos internos de PTFE"**, para que los filamentos puedan guiarse hacia el bloque calefactor para fundirse.
1. No extraiga **"tubos internos de PTFE"** del hotend M4V6, de lo contrario, hilos finos entrarán en el aislador caliente y bloquearán el extremo caliente.
2. Asegúrese de que los **"tubos internos de PTFE"** se hayan insertado en la parte inferior del extremo caliente; de lo contrario, puede causar un **problema de bloqueo del extremo caliente** (mucho filamento que ingresa al aislamiento térmico bloqueará el extremo caliente). o **"problema de cuerdas"** (unos pocos filamentos derretidos en el aislamiento térmico reducirán la eficacia de la retracción).
3. No se recomienda utilizar tuberías de PTFE de colores como **"tubo interior de PTFE"** porque su rendimiento de resistencia a la temperatura es deficiente.
##### :pushpin: Si desea comprender mejor el hotend M4V6, consulte la siguiente imagen:
- [:art: Estructura del conjunto Hotend M4V6](2.jpg)  
- [:art: Estructura del hotend M4V6](1.jpg)


#### :warning: Debe cargar 4 filamentos en el hotend M4V6 simultáneamente.


-----
## <a id="pt">Precauções para usar M4V6</a> [:arrow_heading_up:](#choose-language)
### Cuidados :bangbang: 
A M4V6 pertence a uma ***extrusora Bowden***. ***Extrusora Bowden*** refere-se a uma estrutura de extrusora que separa a **extrusora** (dispositivo alimentador de filamento) e a **"extremidade quente"** (dispositivo de fusão de filamento). Essa estrutura pode efetivamente reduzir o peso da cabeça de impressão, que é comumente usada em impressoras 3D multicoloridas.
     

        A. Filamento            B. Extrusora (alimentador de filamento) C. Tubo de alimentação D. Conector do tubo PTFE
        E. Tubo interno de PTFE F. M4V6 Hotend                          G. Bico

#### :warning: Deve-se conectar as extrusoras ao hotend M4V6 usando tubos.
Deve-se usar tubos para conectar a extrusora aos conectores no hot end M4V6, para que os filamentos possam ser empurrados para dentro do hot end.
Os tubos requerem a utilização de materiais mais duros e o interior deve ser muito liso. Atualmente, **tubos de PTFE** são comumente usados. Não use tubos de borracha ou PVC.


#### :warning: NÃO puxe os “tubos internos de PTFE” do hotend M4V6.
O hot end M4V6 usa quatro tubos de PTFE brancos inseridos no bloco de aquecimento do hot end, que são chamados de **"tubos internos de PTFE"**, para que os filamentos possam ser guiados para dentro do bloco de aquecimento para fusão.
1. Não puxe **"tubos internos de PTFE"** para fora do hotend M4V6, caso contrário, fios finos entrarão no isolador quente e bloquearão o hotend.
2. Certifique-se de que os **"tubos internos de PTFE"** foram inseridos na parte inferior da extremidade quente, caso contrário, isso pode causar **problema de bloqueio da extremidade quente** (muito filamento entrando no isolamento térmico bloqueará a extremidade quente) ou **"problema de cordas"** (alguns filamentos derretidos no isolamento térmico reduzirão a eficácia da retração).
3. Não é recomendado usar tubos de PTFE coloridos como **"tubo de PTFE interno"** porque seu desempenho de resistência à temperatura é baixo.  
##### :pushpin: Se você quiser entender melhor o hotend M4V6, consulte a imagem a seguir:
- [:art: Estrutura da montagem do Hotend M4V6](2.jpg)  
- [:art: Estrutura do Hotend M4V6](1.jpg)


#### :warning: Deve carregar 4 filamentos no hotend M4V6 simultaneamente.


----
## <a id="fr">Précautions d'utilisation de M4V6</a> [:arrow_heading_up:](#choose-language)
### Précautions :bangbang: 
Le M4V6 appartient à une ***extrudeuse Bowden***. ***L'extrudeuse Bowden*** fait référence à une structure d'extrudeuse qui sépare l'**extrudeuse** (dispositif d'alimentation en filament) et la **« extrémité chaude »** (dispositif de fusion de filament). Cette structure peut réduire efficacement le poids de la tête d'impression, couramment utilisée dans les imprimantes 3D multicolores.
     

     A. Filament    B. Extrudeuse (alimentateur de filament)    C. Tuyau d'alimentation     D. Connecteur de tube PTFE
     E. Tube intérieur en PTFE F. M4V6 Hotend   G. Buse

#### :warning: Doit connecter les extrudeuses au hotend M4V6 à l'aide de tuyaux.
Il faut utiliser des tuyaux pour connecter l'extrudeuse aux connecteurs de l'extrémité chaude du M4V6, afin que les filaments puissent être poussés dans l'extrémité chaude.
Les tuyaux nécessitent l’utilisation de matériaux plus durs et l’intérieur doit être très lisse. Actuellement, les **tubes PTFE** sont couramment utilisés. N'utilisez pas de tubes en caoutchouc ou en PVC.


#### :warning: NE retirez PAS les "tubes internes en PTFE" du hotend M4V6.
Le hot end M4V6 utilise quatre tubes PTFE blancs insérés dans le bloc chauffant du hot end, appelés **"tubes PTFE internes"**, afin que les filaments puissent être guidés dans le bloc chauffant pour fondre.
1. Ne retirez pas les **"tubes internes en PTFE"** du hotend M4V6, sinon des fils fins entreront dans l'isolateur chaud et bloqueront l'extrémité chaude.
2. Assurez-vous que les **"tubes internes en PTFE"** ont été insérés dans le bas de l'extrémité chaude, sinon cela pourrait provoquer un **problème de blocage de l'extrémité chaude** (une grande partie du filament entrant dans l'isolation thermique bloquera l'extrémité chaude). ou **"problème de cordes"** (quelques filaments fondus dans l'isolation thermique réduiront l'efficacité de la rétraction).
3. Il n'est pas recommandé d'utiliser des tuyaux en PTFE colorés comme ** « tube intérieur en PTFE » ** car leurs performances de résistance à la température sont médiocres. 
##### :pushpin: Si vous souhaitez mieux comprendre le hotend M4V6, veuillez vous référer à l'image suivante :
- [:art: Structure de l'assemblage M4V6 Hotend](2.jpg)  
- [:art: Structure du M4V6 Hotend](1.jpg)


#### :warning: Doit charger 4 filaments simultanément sur le hotend M4V6.


-----
## <a id="de">Vorsichtsmaßnahmen für die Verwendung von M4V6</a> [:arrow_heading_up:](#choose-language)
### Vorsichtsmaßnahmen :bangbang:
Der M4V6 gehört zu einem ***Bowden-Extruder***. ***Bowden-Extruder*** bezieht sich auf eine Extruderstruktur, die den **Extruder** (Filamentzuführgerät) und das **„heiße Ende“** (Filamentschmelzgerät) trennt. Durch diese Struktur kann das Gewicht des Druckkopfs, der häufig in Mehrfarben-3D-Druckern verwendet wird, effektiv reduziert werden.
     

    A. Filament              B. Extruder (Filamentzuführung)    C. Zufuhrrohr   D. PTFE-Schlauchverbinder
    E. Innerer PTFE-Schlauch F. M4V6 Hotend                     G. Düse

#### :warning: Die Extruder müssen über Rohre mit dem M4V6-Hotend verbunden werden.
Es müssen Rohre verwendet werden, um den Extruder mit den Anschlüssen am M4V6-Hot-End zu verbinden, damit die Filamente in das Hot-End gedrückt werden können.
Die Rohre erfordern den Einsatz härterer Materialien und die Innenseite sollte sehr glatt sein. Derzeit werden häufig **PTFE-Schläuche** verwendet. Verwenden Sie keine Gummi- oder PVC-Schläuche.


#### :warning: Ziehen Sie NICHT die „inneren PTFE-Schläuche“ aus dem M4V6-Hotend heraus.
Das M4V6-Hot-End verwendet vier weiße PTFE-Röhren, die in den Heizblock des Hot-Ends eingeführt werden und als „innere PTFE-Röhren“ bezeichnet werden, damit die Filamente zum Schmelzen in den Heizblock geführt werden können.
1. Ziehen Sie die **„inneren PTFE-Schläuche“** nicht aus dem M4V6-Hotend heraus, da sonst feine Gewinde in den heißen Isolator gelangen und das heiße Ende blockieren.
2. Stellen Sie sicher, dass die **„inneren PTFE-Schläuche“** in die Unterseite des heißen Endes eingeführt wurden, andernfalls kann es zu einem **Problem mit blockiertem heißen Ende** kommen (viel Filament, das in die Wärmeisolierung eindringt, blockiert das heiße Ende). oder **„Problem mit den Saiten“** (einige in der Wärmeisolierung geschmolzene Filamente verringern die Wirksamkeit des Rückzugs).
3. Es wird nicht empfohlen, farbige PTFE-Rohre als **„inneres PTFE-Rohr“** zu verwenden, da ihre Temperaturbeständigkeit schlecht ist. 
##### :pushpin: Wenn Sie das M4V6-Hotend besser verstehen möchten, sehen Sie sich bitte das folgende Bild an:
- [:art: Struktur der M4V6 Hotend-Baugruppe](2.jpg)  
- [:art: Struktur des M4V6 Hotends](1.jpg)


#### :warning: Es müssen 4 Filamente gleichzeitig auf das M4V6-Hotend geladen werden.


----
## <a id="it">Precauzioni per l'utilizzo di M4V6</a> [:arrow_heading_up:](#choose-language)
### Avvertenze :bangbang:
L'M4V6 appartiene ad un ***estrusore Bowden***. ***Estrusore Bowden*** si riferisce a una struttura dell'estrusore che separa l'**estrusore** (dispositivo di alimentazione del filamento) e l'**"hot end"** (dispositivo di fusione del filamento). Questa struttura può ridurre efficacemente il peso della testina di stampa, comunemente utilizzata nelle stampanti 3D multicolori.    
     

        A. Filamento    B. Estrusore (alimentatore di filamento)    C. Tubo di alimentazione    D. Connettore del tubo in PTFE
        E. Tubo interno in PTFE     F. Hotend M4V6  G. Ugello

#### :warning: È necessario collegare gli estrusori all'hotend M4V6 utilizzando un tubo.
È necessario utilizzare tubi per collegare l'estrusore ai connettori sull'hot end M4V6, in modo che i filamenti possano essere spinti nell'hot end.
I tubi richiedono l'uso di materiali più duri e l'interno deve essere molto liscio. Attualmente vengono comunemente utilizzati i **tubi in PTFE**. Non utilizzare tubi in gomma o PVC.      


#### :warning: NON estrarre i "tubi interni in PTFE" dall'hotend M4V6.
L'hotend M4V6 utilizza quattro tubi in PTFE bianchi inseriti nel blocco riscaldante dell'hotend, chiamati **"tubi interni in PTFE"**, in modo che i filamenti possano essere guidati nel blocco riscaldante per la fusione.
1. Non estrarre i **"tubi interni in PTFE"** dall'hotend M4V6, altrimenti fili sottili entreranno nell'isolatore caldo e bloccheranno l'hotend.
2. Assicurarsi che i **"tubi interni in PTFE"** siano stati inseriti nella parte inferiore dell'hot end, altrimenti potrebbe verificarsi un **problema di blocco dell'hot end** (molto filamento che entra nell'isolamento termico bloccherà l'hot end) o **"problema delle corde"** (alcuni filamenti fusi nell'isolamento termico ridurranno l'efficacia della retrazione).
3. Non è consigliabile utilizzare tubi in PTFE colorati come **"tubo interno in PTFE"** perché le loro prestazioni di resistenza alla temperatura sono scarse.     
##### :pushpin: Se desideri comprendere meglio l'hotend M4V6, fai riferimento alla seguente immagine:
- [:art: Struttura dell'assemblaggio Hotend M4V6](2.jpg)  
- [:art: Struttura dell'hotend M4V6](1.jpg)


#### :warning: È necessario caricare 4 filamenti sull'hotend M4V6 contemporaneamente.


----
## <a id="ru">Меры предосторожности при использовании M4V6</a> [:arrow_heading_up:](#choose-language)
### Предостережения :bangbang:
M4V6 принадлежит ***экструдеру Боудена***. ***Экструдером Боудена*** называется конструкция экструдера, в которой разделены **экструдер** (устройство подачи нити) и **"горячий конец"** (устройство плавления нити). Эта структура может эффективно снизить вес печатающей головки, которая обычно используется в многоцветных 3D-принтерах.
     

        A. Нить                        B. Экструдер (податчик нити) C. Подающая труба D. Соединитель трубки из ПТФЭ
        E. Внутренняя трубка из ПТФЭ   F. M4V6 Hotend               G. Сопло

#### :warning: Необходимо соединить экструдеры с хотэндом M4V6 с помощью труб.
Необходимо использовать трубы для подключения экструдера к разъемам на хотэнде M4V6, чтобы нити можно было протолкнуть в хотэнд.
Трубы требуют использования более твердых материалов, а внутренняя поверхность должна быть очень гладкой. В настоящее время широко используются **трубки из ПТФЭ**. Не используйте резиновые или ПВХ трубки.


#### :warning: НЕ вытягивайте «внутренние трубки из ПТФЭ» из хотэнда M4V6.
В хотэнде M4V6 используются четыре белые трубки из ПТФЭ, вставленные в нагревательный блок горячего конца, которые называются **"внутренними трубками из ПТФЭ"**, так что нити можно направить в нагревательный блок для плавления.
1. Не вытягивайте **"внутренние трубки из ПТФЭ"** из горячего конца M4V6, иначе тонкая резьба попадет в горячий изолятор и заблокирует горячий конец.
2. Убедитесь, что **"внутренние трубки из ПТФЭ"** вставлены в нижнюю часть горячего конца, в противном случае это может вызвать **проблему с блокировкой горячего конца** (большая часть нити, попадающая в теплоизоляцию, заблокирует горячий конец) или **"проблема со струнами"** (несколько нитей, расплавившихся в теплоизоляции, снизят эффективность втягивания).
3. Не рекомендуется использовать цветные трубы из ПТФЭ в качестве **"внутренней трубки из ПТФЭ"**, поскольку их термостойкость низкая.  
##### :pushpin: Если вы хотите лучше понять хотэнд M4V6, обратитесь к следующему изображению:
- [:art: Структура узла Hotend M4V6](2.jpg)  
- [:art: Структура хотенда M4V6](1.jpg)


#### :warning: Необходимо одновременно загрузить 4 нити на хотэнд M4V6.


----
## <a id="jp">M4V6使用上の注意</a> [:arrow_heading_up:](#choose-language)
### 注意事項 :bangbang:
M4V6 は ***Bowden 押出機*** に属します。 ***ボーデン押出機*** は、**押出機** (フィラメント供給装置) と **「ホットエンド」** (フィラメント溶融装置) を分離する押出機の構造を指します。 この構造により、多色 3D プリンタで一般的に使用されるプリントヘッドの重量を効果的に軽減できます。    
     

        A. フィラメント             B. エクストルーダー (フィラメントフィーダー)    C. 供給パイプ      D. PTFE チューブコネクター
        E. インナー PTFE チューブ   F. M4V6 ホットエンド                         G. ノズル

#### :warning: パイプを使用して押出機と M4V6 ホットエンドを接続する必要があります。
フィラメントをホットエンドに押し込めるように、パイプを使用して押出機を M4V6 ホットエンドのコネクタに接続する必要があります。
パイプにはより硬い材料を使用する必要があり、内部は非常に滑らかでなければなりません。 現在、**PTFE チューブ** が一般的に使用されています。 ゴムチューブやPVCチューブは使用しないでください。     


#### :warning: M4V6 ホットエンドから「内側 PTFE チューブ」を引き抜かないでください。
M4V6 ホットエンドは、**「インナー PTFE チューブ」** と呼ばれる、ホットエンドの加熱ブロックに挿入された 4 本の白色 PTFE チューブを使用しており、フィラメントを加熱ブロックに誘導して溶融させることができます。
1. **「内側 PTFE チューブ」** を M4V6 ホットエンドから引き抜かないでください。そうしないと、細い糸がホットアイソレーターに入り、ホットエンドをブロックします。
2. **「内側 PTFE チューブ」** がホットエンドの底部に挿入されていることを確認してください。挿入されていないと、**ホットエンドのブロック問題** が発生する可能性があります (断熱材に多くのフィラメントが入り込むとホットエンドがブロックされます)。 または **「ストリングの問題」** (断熱材内で溶けたフィラメントが数本あると、収縮効果が低下します)。
3. カラー PTFE パイプを **「インナー PTFE チューブ」** として使用することは、耐熱性能が劣るため推奨されません。
##### :pushpin: M4V6 ホットエンドについてさらに詳しく知りたい場合は、次の画像を参照してください。
- [:art: M4V6ホットエンドアセンブリの構造](2.jpg)  
- [:art: M4V6ホットエンドの構造](1.jpg)


#### :warning: 4 つのフィラメントを M4V6 ホットエンドに同時にロードする必要があります。


----
## <a id="kr">M4V6 사용 시 주의사항</a> [:arrow_heading_up:](#choose-language)
### 주의사항 :bangbang:
M4V6은 ***Bowden 압출기***에 속합니다. ***보우덴 압출기***는 **압출기**(필라멘트 공급 장치)와 **"핫 엔드"**(필라멘트 용해 장치)를 분리한 압출기 구조를 말합니다. 이러한 구조는 멀티 컬러 3D 프린터에 일반적으로 사용되는 프린트 헤드의 무게를 효과적으로 줄일 수 있습니다.
     

        A. 필라멘트         B. 압출기(필라멘트 공급 장치)    C. 공급 파이프     D. PTFE 튜브 커넥터
        E. 내부 PTFE 튜브   F. M4V6 핫엔드                  G. 노즐

#### :warning: 파이프를 사용하여 압출기를 M4V6 핫엔드와 연결해야 합니다.
필라멘트를 핫 엔드로 밀어 넣을 수 있도록 파이프를 사용하여 압출기를 M4V6 핫 엔드의 커넥터에 연결해야 합니다.
파이프는 더 단단한 재료를 사용해야 하며 내부는 매우 매끄러워야 합니다. 현재는 **PTFE 튜브**가 많이 사용됩니다. 고무나 PVC 튜브를 사용하지 마세요.


#### :warning: M4V6 핫엔드에서 "내부 PTFE 튜브"를 당기지 마십시오.
M4V6 핫 엔드는 핫 엔드의 가열 블록에 삽입된 4개의 흰색 PTFE 튜브(**"내부 PTFE 튜브"**라고 함)를 사용하여 필라멘트가 용융을 위해 가열 블록으로 안내될 수 있습니다.
1. M4V6 핫엔드에서 **"내부 PTFE 튜브"**를 당기지 마십시오. 그렇지 않으면 미세한 나사산이 핫 아이솔레이터로 들어가 핫 엔드를 차단합니다.
2. **"내부 PTFE 튜브"**가 핫 엔드 바닥에 삽입되었는지 확인하십시오. 그렇지 않으면 **핫 엔드 막힘 문제**가 발생할 수 있습니다(단열재에 들어가는 많은 필라멘트가 핫 엔드를 차단함). 또는 **"끈 문제"**(단열재에 몇 개의 필라멘트가 녹아 수축 효과가 감소합니다).
3. 유색 PTFE 파이프를 **"내부 PTFE 튜브"**로 사용하는 것은 온도 저항 성능이 낮기 때문에 권장하지 않습니다. 
##### :pushpin: M4V6 핫엔드에 대해 더 잘 이해하고 싶다면 다음 이미지를 참조하세요.
- [:art: M4V6 핫엔드 어셈블리의 구조](2.jpg)  
- [:art: M4V6 핫엔드의 구조](1.jpg)


#### :warning: M4V6 핫엔드에 4개의 필라멘트를 동시에 로드해야 합니다.


----
## <a id="ar">احتياطات استخدام M4V6</a> [:arrow_heading_up:](#choose-language)
### يحذر :bangbang:
ينتمي M4V6 إلى ***Bowden extruder***. ***يشير جهاز بثق Bowden*** إلى بنية الطارد التي تفصل **الطارد** (جهاز تغذية الفتيل) و**"الطرف الساخن"** (جهاز ذوبان الفتيل). هذا الهيكل يمكن أن يقلل بشكل فعال من وزن رأس الطباعة، والذي يستخدم بشكل شائع في الطابعات ثلاثية الأبعاد متعددة الألوان. 
     

        A- خيوط    
        B- الطارد (مغذي الخيوط)
        C- أنبوب التغذية
        D- موصل أنبوب PTFE
        E- أنبوب PTFE الداخلي
        F- M4V6 هوتيند
        G- فوهة

#### :warning: يجب توصيل الطاردات مع M4V6 hotend باستخدام الأنابيب.
يجب استخدام الأنابيب لتوصيل الطارد بالموصلات الموجودة على الطرف الساخن M4V6، بحيث يمكن دفع الخيوط إلى الطرف الساخن.
تتطلب الأنابيب استخدام مواد أكثر صلابة ويجب أن يكون الجزء الداخلي سلسًا للغاية. حاليًا، **أنبوب PTFE** شائع الاستخدام. لا تستخدم الأنابيب المطاطية أو البلاستيكية.


#### :warning: لا تسحب "أنابيب PTFE الداخلية" من نقطة التوصيل الساخنة M4V6.
يستخدم الطرف الساخن M4V6 أربعة أنابيب PTFE بيضاء يتم إدخالها في كتلة التسخين للطرف الساخن، والتي تسمى **"أنابيب PTFE الداخلية"**، بحيث يمكن توجيه الشعيرات إلى كتلة التسخين من أجل الذوبان.
1. لا تسحب **"أنابيب PTFE الداخلية"** من الطرف الساخن M4V6، وإلا ستدخل الخيوط الدقيقة إلى العازل الساخن وتسد الطرف الساخن.
2. تأكد من إدخال **"أنابيب PTFE الداخلية"** في الجزء السفلي من الطرف الساخن، وإلا فقد يتسبب ذلك في **مشكلة انسداد الطرف الساخن** (سيؤدي دخول الكثير من الفتيل إلى العزل الحراري إلى سد الطرف الساخن) أو **"مشكلة في الخيوط"** (القليل من الخيوط المنصهرة في العزل الحراري ستقلل من فعالية التراجع).
3. لا ينصح باستخدام أنابيب PTFE الملونة مثل **"أنبوب PTFE الداخلي"** لأن أداء مقاومتها للحرارة ضعيف.  
##### :pushpin: إذا كنت ترغب في الحصول على فهم أفضل لـ M4V6 hotend، فيرجى الرجوع إلى الصورة التالية:
- [:art: هيكل مجموعة M4V6 Hotend](2.jpg)  
- [:art: هيكل M4V6 Hotend](1.jpg)


#### :warning: يجب تحميل 4 خيوط على M4V6 hotend في وقت واحد.


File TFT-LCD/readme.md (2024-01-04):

### :globe_with_meridians: Choose Language (Translated by google)
(https://github-com.translate.goog/ZONESTAR3D/Upgrade-kit-guide?_x_tr_sl=en&_x_tr_tl=es)
(https://github-com.translate.goog/ZONESTAR3D/Upgrade-kit-guide?_x_tr_sl=en&_x_tr_tl=pt)
(https://github-com.translate.goog/ZONESTAR3D/Upgrade-kit-guide?_x_tr_sl=en&_x_tr_tl=fr)
(https://github-com.translate.goog/ZONESTAR3D/Upgrade-kit-guide?_x_tr_sl=en&_x_tr_tl=de)
(https://github-com.translate.goog/ZONESTAR3D/Upgrade-kit-guide?_x_tr_sl=en&_x_tr_tl=it)
(https://github-com.translate.goog/ZONESTAR3D/Upgrade-kit-guide?_x_tr_sl=en&_x_tr_tl=sv)
(https://github-com.translate.goog/ZONESTAR3D/Upgrade-kit-guide?_x_tr_sl=en&_x_tr_tl=pl)
(https://github-com.translate.goog/ZONESTAR3D/Upgrade-kit-guide?_x_tr_sl=en&_x_tr_tl=da)
(https://github-com.translate.goog/ZONESTAR3D/Upgrade-kit-guide?_x_tr_sl=en&_x_tr_tl=cs)
(https://github-com.translate.goog/ZONESTAR3D/Upgrade-kit-guide?_x_tr_sl=en&_x_tr_tl=hr)
(https://github-com.translate.goog/ZONESTAR3D/Upgrade-kit-guide?_x_tr_sl=en&_x_tr_tl=ro)
(https://github-com.translate.goog/ZONESTAR3D/Upgrade-kit-guide?_x_tr_sl=en&_x_tr_tl=sk)

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

-----
## :file_folder: [LCD-DWIN](./LCD-DWIN/)
4.3" TFT-LCD documents    
    
[**Download 4.3" TFT-LCD documents in one go**](https://downgit.github.io/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)

-----
## :file_folder: [TFTLCD35-MK](./TFTLCD35-MK/) 
3.5" TFT-LCD with Touch screen documents    
    
[**Download 3.5" TFT-LCD documents in one go**](https://downgit.github.io/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)

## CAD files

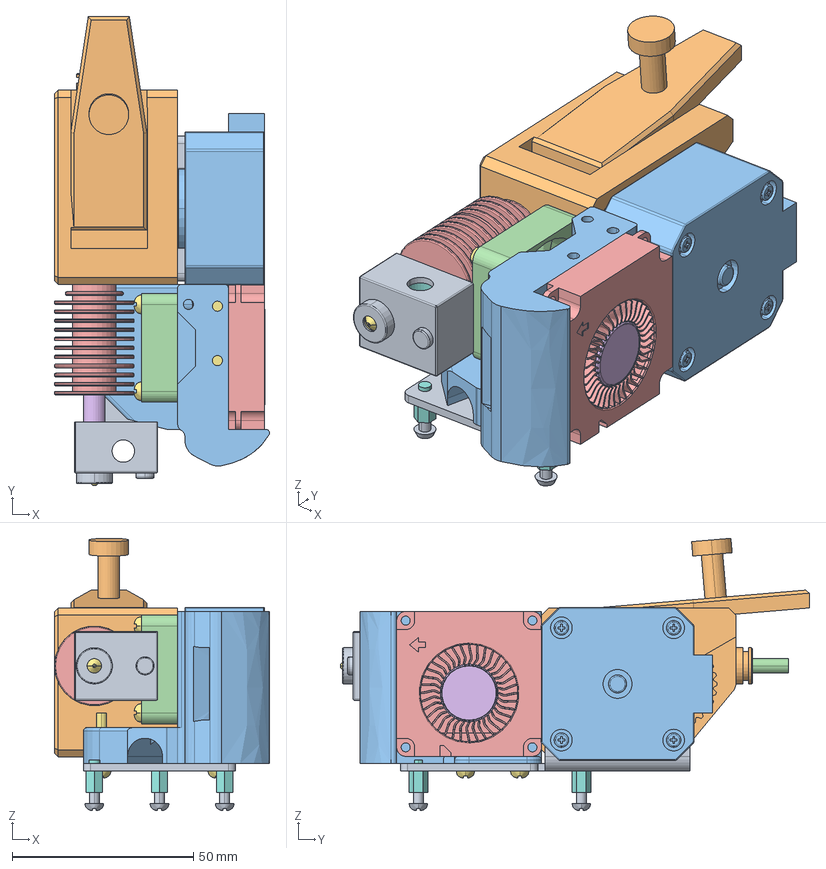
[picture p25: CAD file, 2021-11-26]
Direct_Drive_Extruder/tpuext_v3_asm.stp
59.4 x 129.5 x 75.2 mm
TPUEXT_BR_V1_38
BGM_EXTR_10
42MOTOR_22_2
PT_4X2_AF0_2
HS_D22_L42_M6_3
TH6X26_AF0_5
NZ-E3D_5
HB16X20X12_8
GJT_16X20X12_3
PT_4X2_AF1_2
TPUEXT_PC_V2_4
FAN3010_4
MANIFOLD_SOLID_BREP_51727
MANIFOLD_SOLID_BREP_51947
PM3X16_1 x 6
M3X6_3_2 x 3
PM3X6_3 x 3

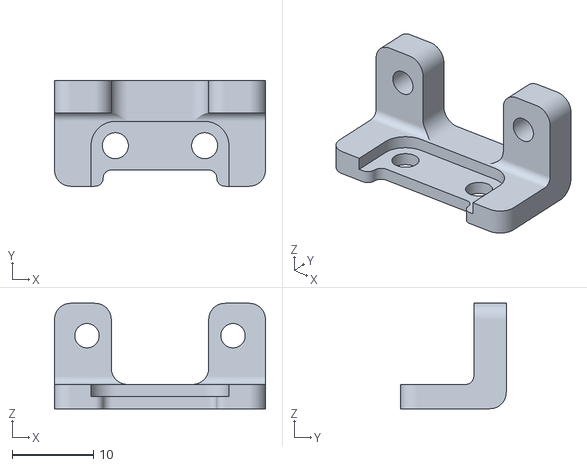
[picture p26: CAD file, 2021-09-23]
Bed_Leveling_Sensor/3DTouch/BLtouch_Bracket.STL
26.0 x 13.0 x 13.0

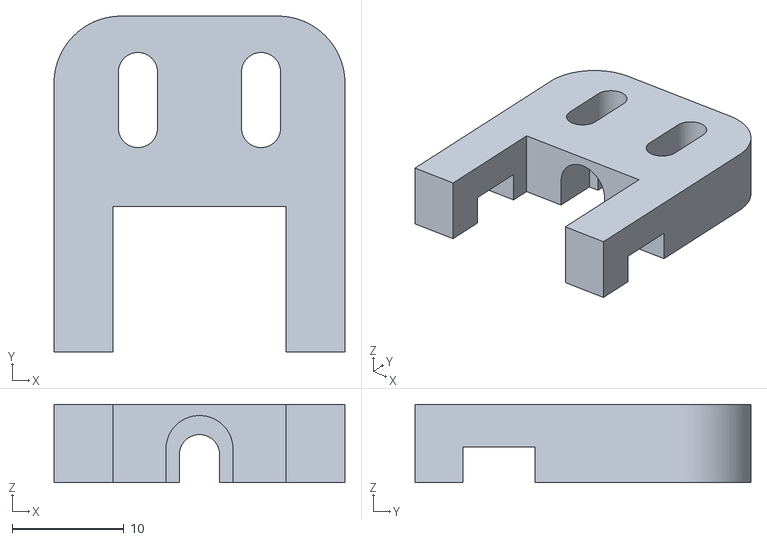
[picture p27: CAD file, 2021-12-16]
Bed_Leveling_Sensor/ZL-Sensor/br_zlsensor_v2.stl
26.0 x 30.0 x 7.00

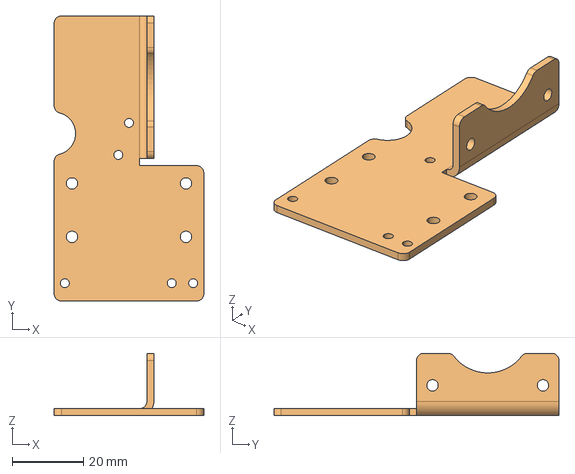
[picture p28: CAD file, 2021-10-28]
Direct_Drive_Extruder/stl/DDE_BR_V1.igs
42.0 x 80.0 x 17.5 mm

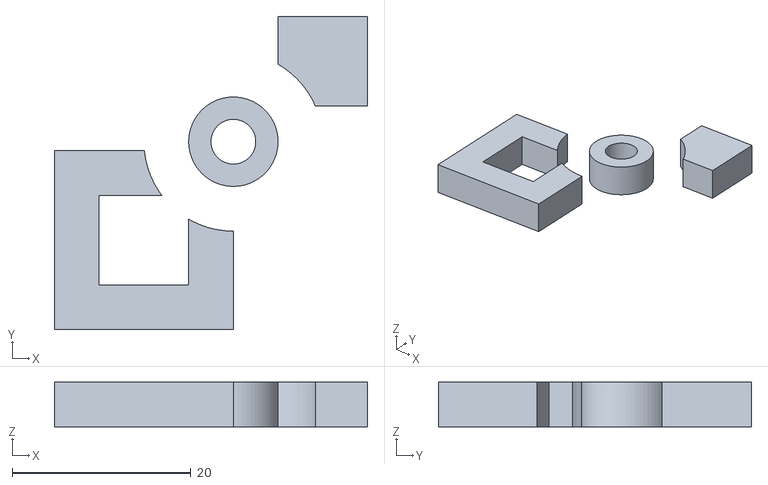
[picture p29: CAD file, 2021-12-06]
HOTEND/E4/example/Cura/4_Color_test/stl/Color_3.stl
35.0 x 35.0 x 5.00

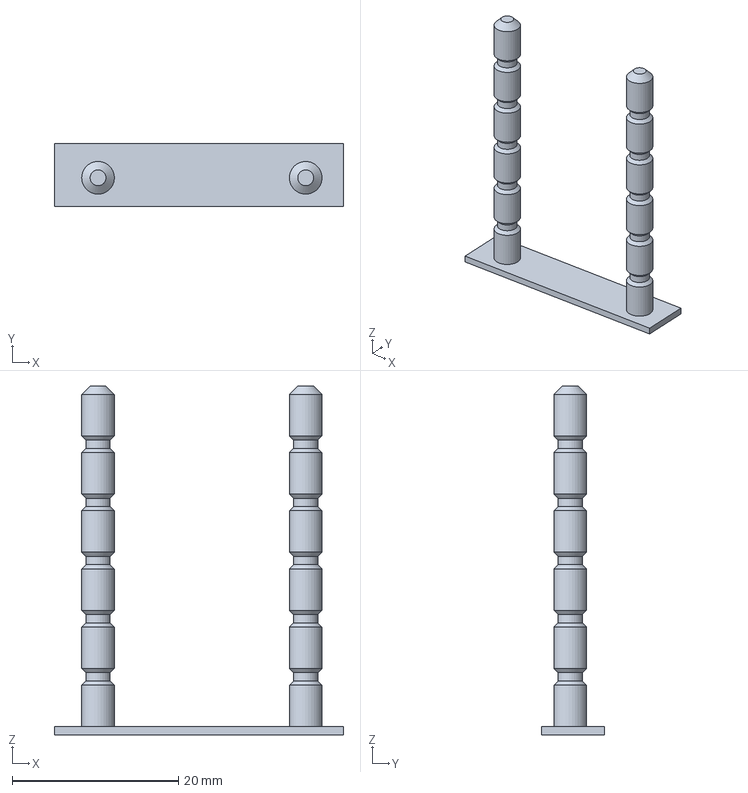
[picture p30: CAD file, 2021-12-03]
HOTEND/E4/example/Cura/Anti_strings_testing/E4_Retraction_Test.3mf
34.8 x 7.57 x 42.0 mm

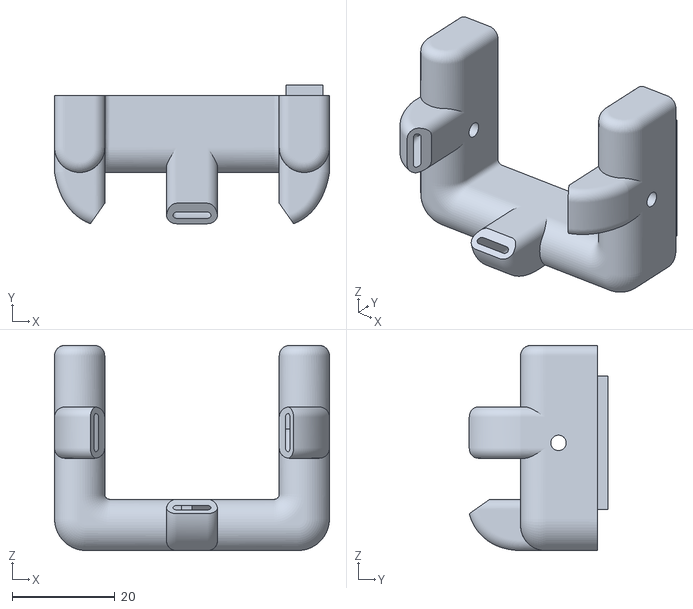
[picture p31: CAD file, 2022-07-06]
HOTEND/E4/Fan_Duct/fan_duct_e4_v3.stl
53.6 x 27.0 x 40.0

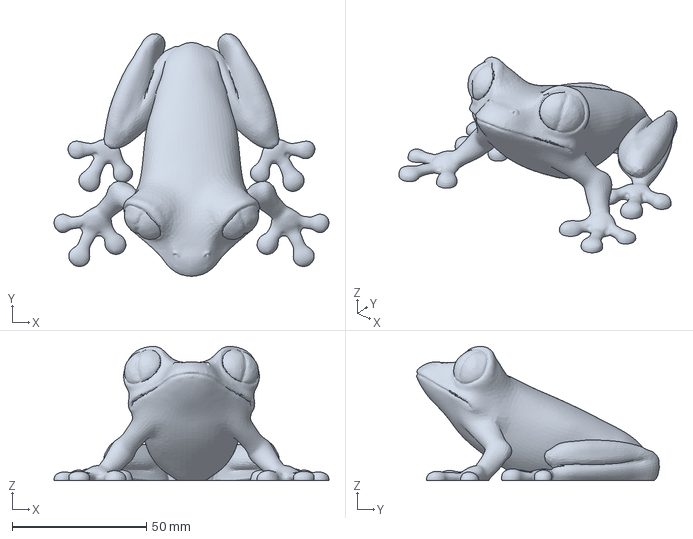
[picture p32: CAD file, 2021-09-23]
HOTEND/M2P1/Example/1c+support/ZM2P1_frog.3mf
102.4 x 90.4 x 50.0 mm

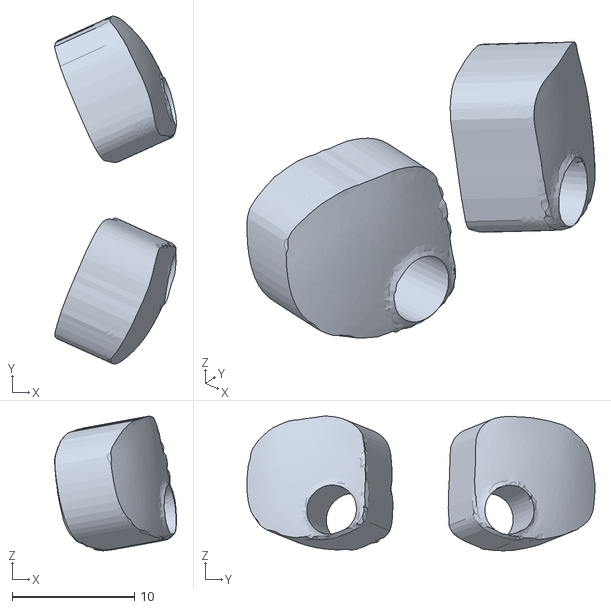
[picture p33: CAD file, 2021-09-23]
HOTEND/M2P1/Example/stl/4C_Niko_Dog_3.stl
10.00 x 28.5 x 11.0

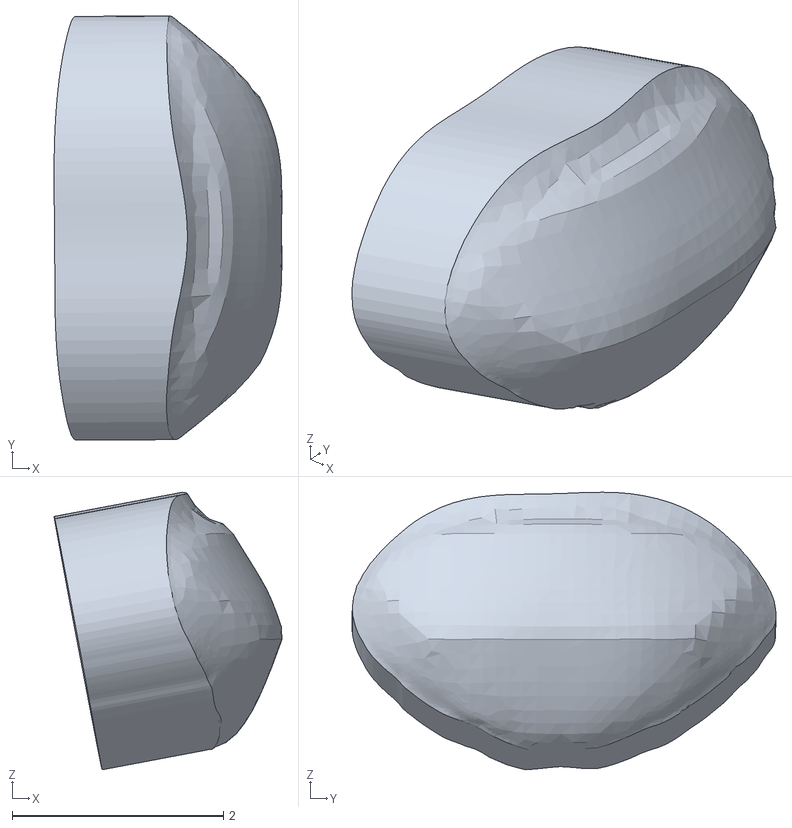
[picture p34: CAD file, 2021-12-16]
HOTEND/M4/Example/5_Color_Rabbit/stl/Nose.stl
2.16 x 4.01 x 2.63

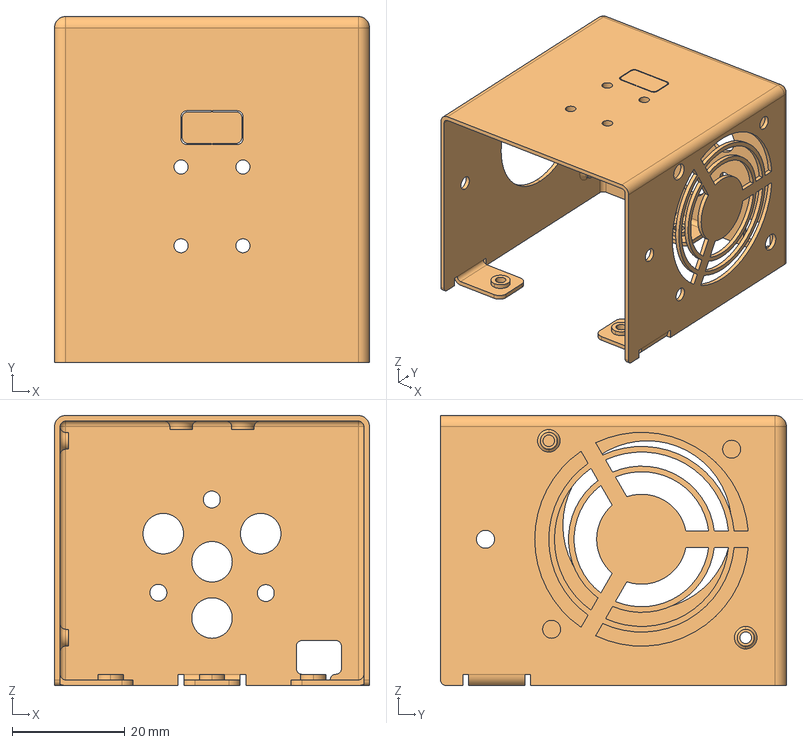
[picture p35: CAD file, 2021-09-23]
HOTEND/M4/M4_V3_V4/HOUSING_M4_V3.stp
56.0 x 61.5 x 48.0 mm

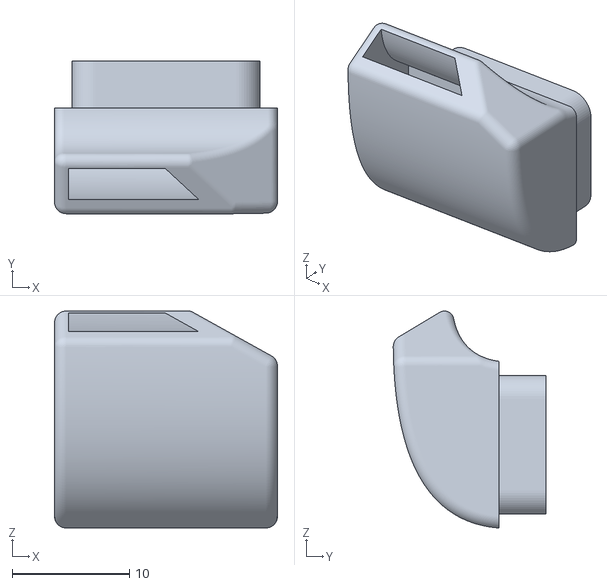
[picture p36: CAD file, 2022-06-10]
HOTEND/Single_color/fanstl/FAN_PHS.stl
19.0 x 13.0 x 18.5

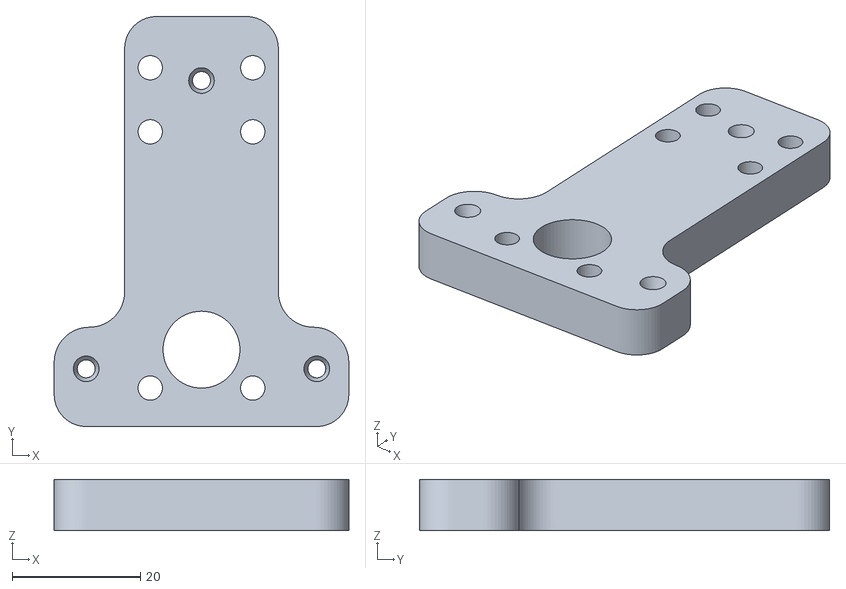
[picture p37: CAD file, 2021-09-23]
Laser_Engraving/inkscape/0. User guide/Bracket stl file for install laser kit/Common/LK25_LK55_BR_V5.stl
46.0 x 64.0 x 8.00

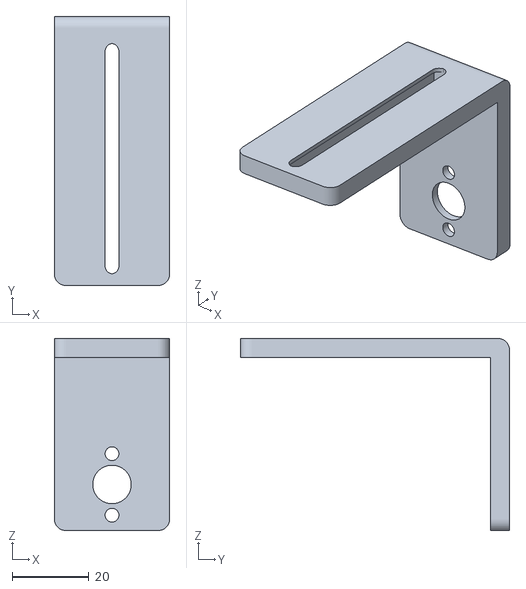
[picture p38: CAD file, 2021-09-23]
Laser_Engraving/inkscape/0. User guide/Bracket stl file for install laser kit/PH-S/LKBR_S_V2.stl
30.0 x 70.0 x 50.0

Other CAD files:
HOTEND/M4/stl/fan_m4v6_v2.stl
Laser_Engraving/inkscape/0. User guide/Bracket stl file for install laser kit/Z6_LK5/lk5_br_z6.stl
Laser_Engraving/inkscape/0. User guide/Bracket stl file for install laser kit/Z8T/M3/LKBR_PHM3V5.stl
Laser_Engraving/inkscape/0. User guide/Bracket stl file for install laser kit/Z8T/M4/LKBR_PHM4.stl
Bed_Leveling_Sensor/ZL-Sensor/br_zlsensor_v1.stl
HOTEND/E4/Fan_Duct/fan_duct_e4_v1.stl
HOTEND/E4/Fan_Duct/fan_duct_e4_v2.stl
HOTEND/E4/Fan_Duct/fanduct_e4_5015.obj
HOTEND/E4/example/Cura/4_Color_test/stl/Color_1.stl
HOTEND/E4/example/Cura/4_Color_test/stl/Color_2.stl
HOTEND/E4/example/Cura/4_Color_test/stl/Color_4.stl
HOTEND/Fan_Duct/5015FAN_S.stl
HOTEND/Fan_Duct/5015fan1.stl
HOTEND/Fan_Duct/FanDuct_4010B_M4V1.stl
HOTEND/Fan_Duct/FanDuct_4010B_common_S.stl
HOTEND/Fan_Duct/FanDuct_5015_M2M3.stl
HOTEND/Fan_Duct/FanDuct_5015_M3V2.stl
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

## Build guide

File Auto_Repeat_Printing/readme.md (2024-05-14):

### :globe_with_meridians: Choose Language (Translated by google)
(https://github-com.translate.goog/ZONESTAR3D/Upgrade-kit-guide?_x_tr_sl=en&_x_tr_tl=es)
(https://github-com.translate.goog/ZONESTAR3D/Upgrade-kit-guide?_x_tr_sl=en&_x_tr_tl=pt)
(https://github-com.translate.goog/ZONESTAR3D/Upgrade-kit-guide?_x_tr_sl=en&_x_tr_tl=fr)
(https://github-com.translate.goog/ZONESTAR3D/Upgrade-kit-guide?_x_tr_sl=en&_x_tr_tl=de)
(https://github-com.translate.goog/ZONESTAR3D/Upgrade-kit-guide?_x_tr_sl=en&_x_tr_tl=it)
(https://github-com.translate.goog/ZONESTAR3D/Upgrade-kit-guide?_x_tr_sl=en&_x_tr_tl=sv)
(https://github-com.translate.goog/ZONESTAR3D/Upgrade-kit-guide?_x_tr_sl=en&_x_tr_tl=pl)
(https://github-com.translate.goog/ZONESTAR3D/Upgrade-kit-guide?_x_tr_sl=en&_x_tr_tl=da)
(https://github-com.translate.goog/ZONESTAR3D/Upgrade-kit-guide?_x_tr_sl=en&_x_tr_tl=cs)
(https://github-com.translate.goog/ZONESTAR3D/Upgrade-kit-guide?_x_tr_sl=en&_x_tr_tl=hr)
(https://github-com.translate.goog/ZONESTAR3D/Upgrade-kit-guide?_x_tr_sl=en&_x_tr_tl=ro)
(https://github-com.translate.goog/ZONESTAR3D/Upgrade-kit-guide?_x_tr_sl=en&_x_tr_tl=sk)

(https://github-com.translate.goog/ZONESTAR3D/Upgrade-kit-guide?_x_tr_sl=en&_x_tr_tl=ru)
(https://github-com.translate.goog/ZONESTAR3D/Upgrade-kit-guide?_x_tr_sl=en&_x_tr_tl=ja)
(https://github-com.translate.goog/ZONESTAR3D/Upgrade-kit-guide?_x_tr_sl=en&_x_tr_tl=ko)
(https://github-com.translate.goog/ZONESTAR3D/Upgrade-kit-guide?_x_tr_sl=en&_x_tr_tl=id)
(https://github-com.translate.goog/ZONESTAR3D/Upgrade-kit-guide?_x_tr_sl=en&_x_tr_tl=th)
(https://github-com.translate.goog/ZONESTAR3D/Upgrade-kit-guide?_x_tr_sl=en&_x_tr_tl=vi)
(https://github-com.translate.goog/ZONESTAR3D/Upgrade-kit-guide?_x_tr_sl=en&_x_tr_tl=iw)
(https://github-com.translate.goog/ZONESTAR3D/Upgrade-kit-guide?_x_tr_sl=en&_x_tr_tl=ar)
(https://github-com.translate.goog/ZONESTAR3D/Upgrade-kit-guide?_x_tr_sl=en&_x_tr_tl=tr)
(https://github-com.translate.goog/ZONESTAR3D/Upgrade-kit-guide?_x_tr_sl=en&_x_tr_tl=el)
(https://github-com.translate.goog/ZONESTAR3D/Upgrade-kit-guide?_x_tr_sl=en&_x_tr_tl=pt)
(https://github-com.translate.goog/ZONESTAR3D/Upgrade-kit-guide?_x_tr_sl=en&_x_tr_tl=zh-CN)

# [Automatic Repeat Printing Module][selllink] User Manual
## :warning: ATTENTION PLEASE :warning: 
#### 1. Before using Automatic Repeat Printing feature, please confirm that the prints is easy to be removed from the printing platform while the hotbed is cooled. For details, please refer to [Important Notice][7]
#### 2. Remove the M84 command from the "End G-code" of "machine setting" of slicing software.

## Contents
* [**1. Brief introduction**][1]  
* [**2. Parts list**][2]
* [**3. Installation**][3]  
* [**4. Wiring**][4]
* [**5. Upgrade firmware**][5] 
* [**6. Verify wiring and installation**][6]  
* [**7. Important Notice**][7]  
* [**8. Workflow of Automatic Repeat Printing**][8]
* [**9. Apply Automatic Repeat Printing function**][9]
* [**10.Example Gcode files**][10]
* [**11.Advanced features**][11]

## 1. Brief introduction   [return to contents>>][0]
Sometimes we hope to use the 3D printer to make some plastic parts in small quantities (dozens or hundreds). In this case, we need a device to automatically remove the 3D printed object on the hot bed and print this part repeatedly, so that the 3D printer can realize unattended automatic repeated production.  [**Automatic Repeat Printing Module**][selllink] is an upgrade kit for Z9 to meet this requirement.     
**The premise that the [Automatic Repeat Printing Module][selllink] can work normally is that the printed 3D printed object can be easily separated from the printing platform after the printing platform is cooled.** According to our test, if we were used the [PEI spring printing][PEIselllink] platform and properly set the printing height of the first layer, the printed object (made by ABS, PLA+ or PETG filament etc.) can be easily separated from the platform after the heat bed is cooled to below 25℃.    
The **[Automatic Repeat Printing Module][selllink]** is composed of **Arm Drivers, lead screw fixing blocks, lead screws and Pushing-arm**. It is installed between the hot bed and the hot end. 
The working process is that finished one print first, then cooling the printing platform, and then push the printed object out of the printing platform with the Pushing-arm, and then print the next one repeatedly.  
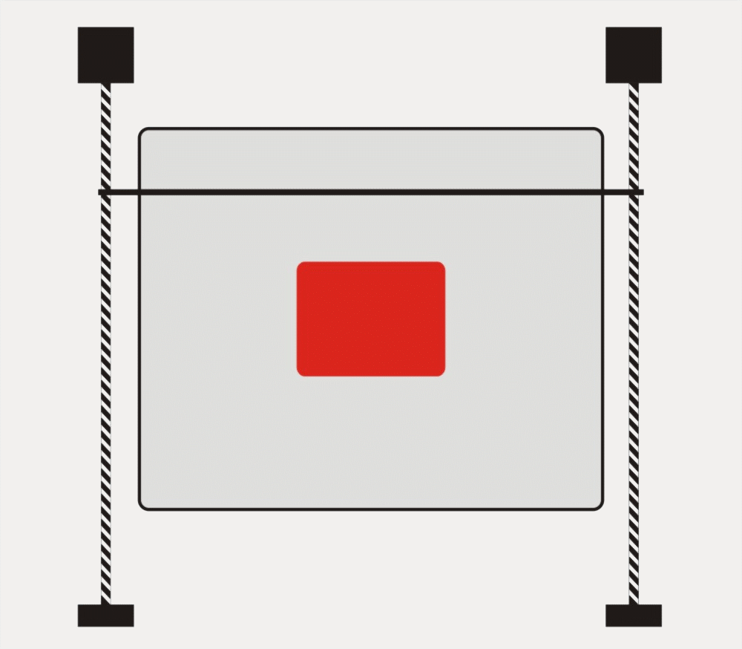
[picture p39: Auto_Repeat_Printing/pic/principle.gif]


## 2. Parts list   [return to contents>>][0]  
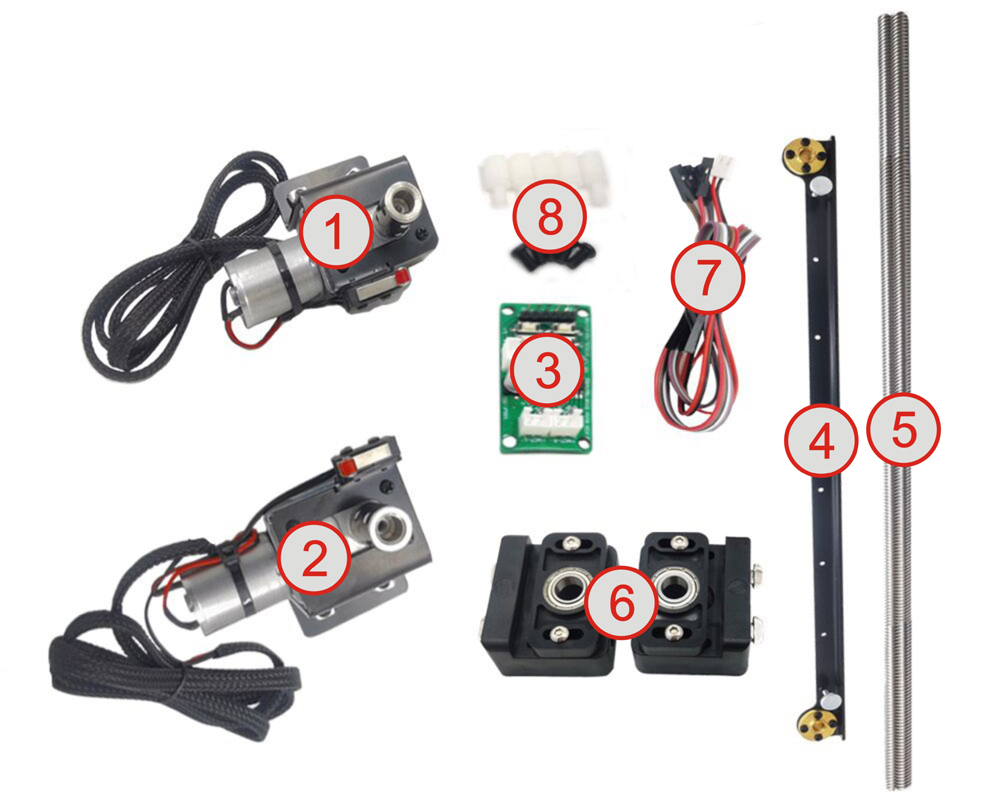
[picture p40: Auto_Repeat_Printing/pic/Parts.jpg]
    
* **Left Arm Driver Assembly with limit switch(1).**    
* **Right Arm Driver Assembly with limit switch(2).**   
* **Drive board(3).**     
* **Pushing-Arm(4).**   
* **lead screws(5).**    
* **Lead Screw Fixing Blocks(6).**   
* **1 x 6Pin DuPont wire, 1 x 2Pin power wire with connector(7).**   
* **4 x M3x6 screws + 4x M3 Nylon pillar(8).**    

## 3. Installation   [return to contents>>][0]
### 3.1 Install the arm driver assemblies.
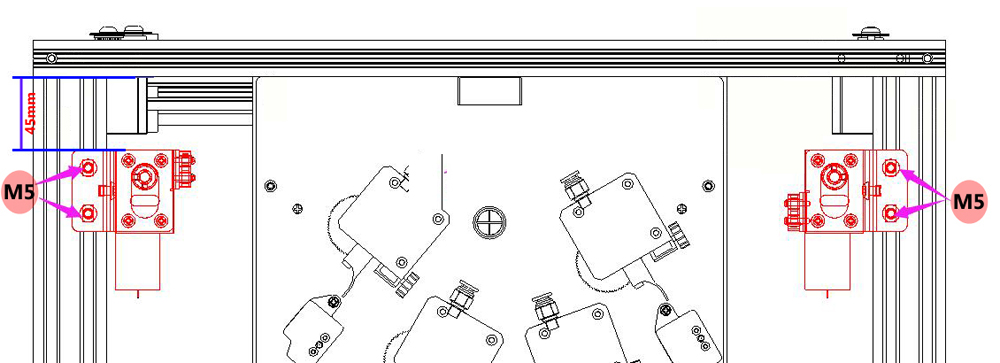
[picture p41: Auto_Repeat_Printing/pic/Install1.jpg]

###  3.2 Install lead screw fixing blocks.
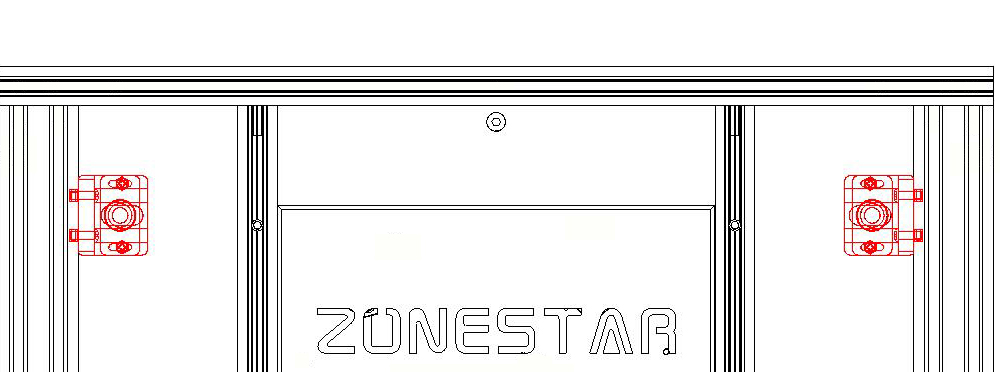
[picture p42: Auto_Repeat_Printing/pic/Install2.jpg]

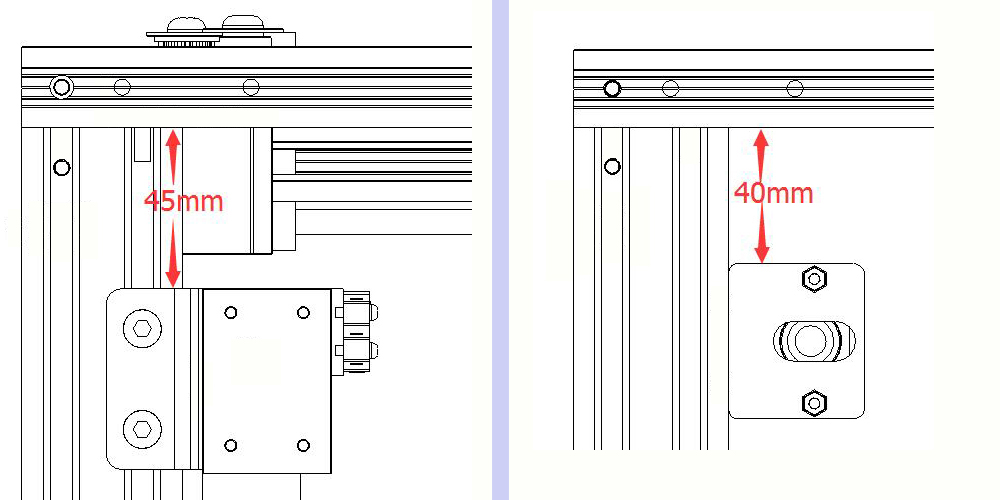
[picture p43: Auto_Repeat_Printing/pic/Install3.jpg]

###  3.3 Install Pushing-arm and lead screws.
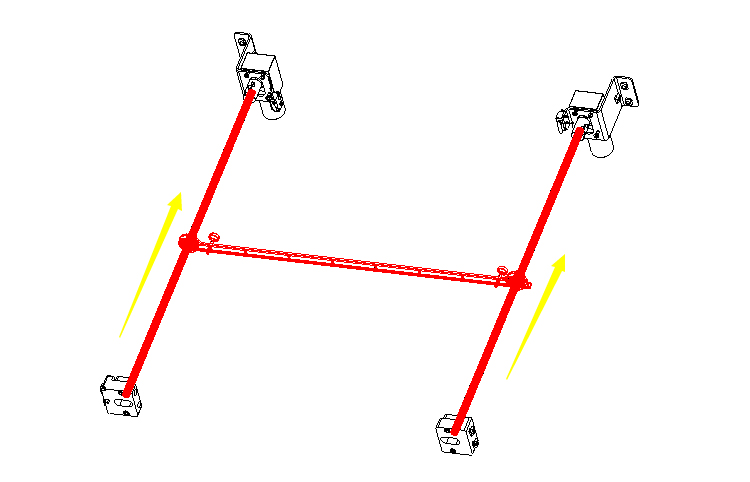
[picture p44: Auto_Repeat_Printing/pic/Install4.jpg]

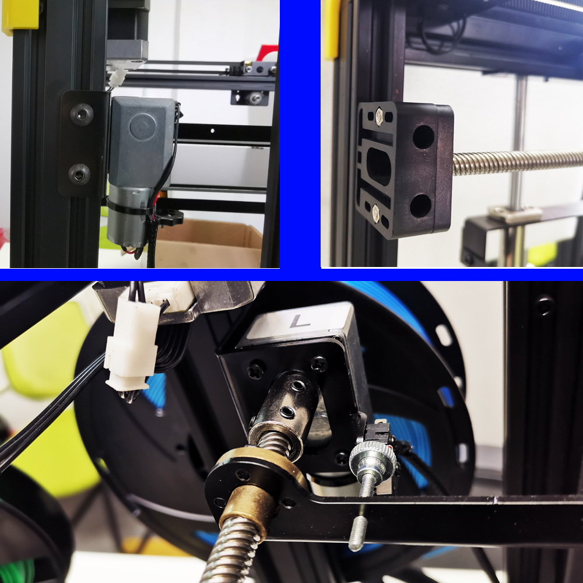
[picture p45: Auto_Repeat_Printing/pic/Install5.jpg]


## 4. Wiring   [return to contents>>][0]
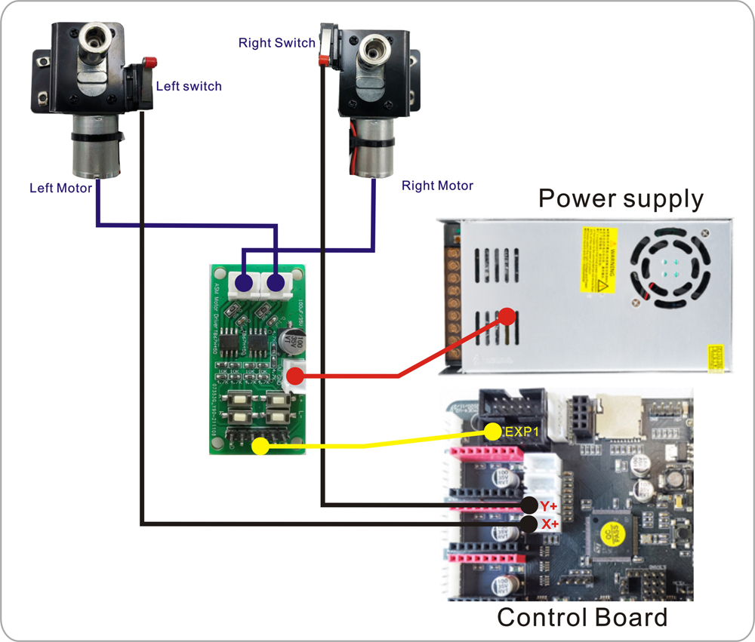
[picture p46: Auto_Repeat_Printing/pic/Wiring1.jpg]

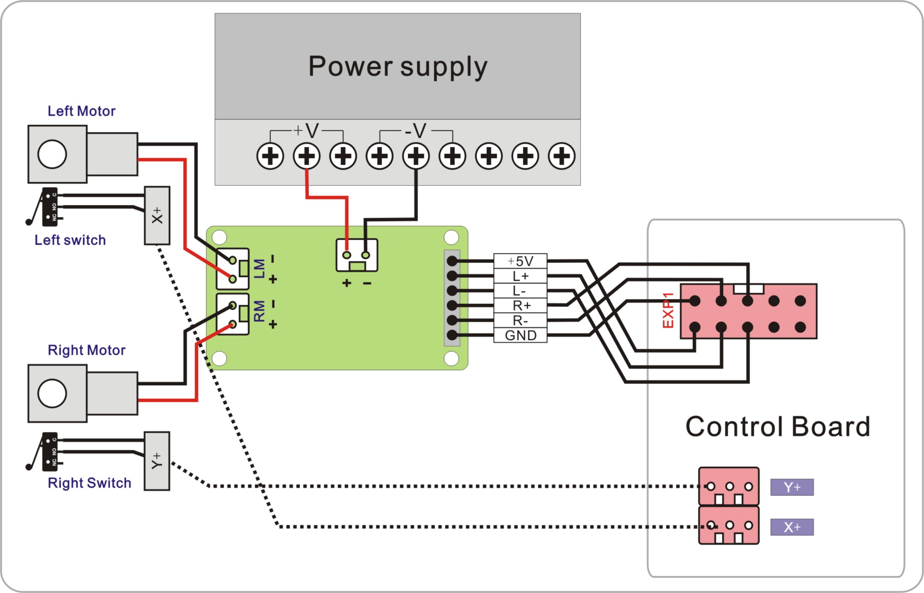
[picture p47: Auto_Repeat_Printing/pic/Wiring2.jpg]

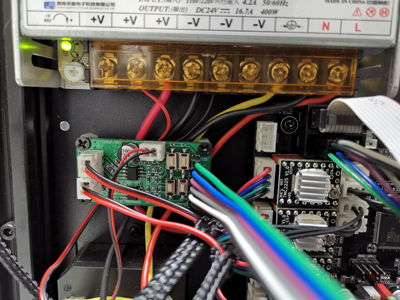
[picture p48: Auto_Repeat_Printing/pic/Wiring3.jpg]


## 5. Upgrade firmware   [return to contents>>][0]
Download firmware bin file and upload to your 3d printer.
- [**Z9V5-MK6**](https://github.com/ZONESTAR3D/Firmware/tree/master/Z9/Z9V5/bin/Z9V5Pro-MK6/customized)   
- [**Z9V5-MK4 & Z9V5-MK5**](https://github.com/ZONESTAR3D/Firmware/tree/master/Z9/Z9V5/bin/Z9V5Pro-MK4/customized) 
- [**Z9V5-MK3**](https://github.com/ZONESTAR3D/Firmware/tree/master/Z9/Z9V5/bin/Z9V5Pro-MK3/customized)   
- [**Z9V5-MK1 & Z9V5-MK2**](https://github.com/ZONESTAR3D/Firmware/tree/master/Z9/Z9V5/bin/Z9V5Pro-MK6/customized)   
- [**Z9M4**](https://github.com/ZONESTAR3D/Firmware/tree/master/Z9/Z9M4/ZM3E4/Firmware/Special)  

>**How to upload firmware**  
> 1. Download the zip file and unzip it, you will get a "firmware.bin" file.  
> 2. Copy "firmware.bin" to the root directory of Micro-SD card.   
> **NOTE:if there is a "old_fw.bin" in the SD card, delete it first.** 
> 3. Power off 3d printer and plug the SD card into card socket of control board.
> 4. Power on the printer, push the power button and wait about 30 seconds.  
> 5. Do the below step on LCD screen to initialize EEPROM after uploaded firmware:  
>   `MENU: Control>>Restore Defaults`  
> 6. Check the firmware version on LCD screen:    
> 	`MENU: Infor>>Firmware Version` 

## 6. Verify wiring and installation   [return to contents>>][0]
* **Step 1**: Power on the 3d printer.  
* **Step 2**: Push the buttons on the drive board, and check if the motor rotate as below:
	* **Click L+ button**: the left motor rotate clockwise.
	* **Click L- button**: the left motor rotate anti-clockwise.
	* **Click R+ button**: the right motor rotate clockwise.
	* **Click R- button**: the right motor rotate anti-clockwise.
* **Step 3**: Operature the LCD MENU: ***Control>>Repeat Print***
	* **ATTENTION: Make sure the arm is above the hot bed before testing**
	* Move to MENU ***Repeat Printing:*** and click knob to turn ***Repeat Printing: ON***.
	* Move to MENU ***Home Arm Test***, click knob, the arm will move back and stop when the ENDSTOPs it triggered.
	* Move to MENU ***Push Arm Test***, click knob, the arm will move front 340mm.

## 7. Important Notice   [return to contents>>][0]
* Before using Automatic Repeat Printing feature, please confirm that the printed object is easy to be removed from the printing platform while the hotbed is cooled. It is recommended that you print and confirm this before using Automatic Repeat Printing. 

## 8. Workflow of Automatic Repeat Printing   [return to contents>>][0]
A complete workflow of repeated printing is:   
**[Print]->[Wait bed cool]->[Move up hotbed]->[Push the arm]->[Home the arm]->[Print next one]**.     
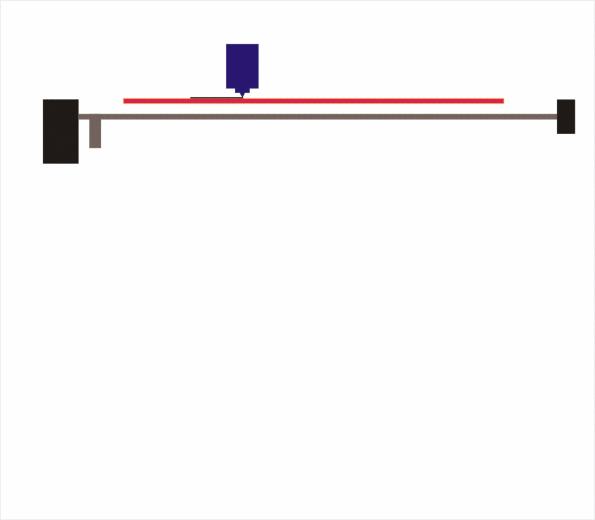
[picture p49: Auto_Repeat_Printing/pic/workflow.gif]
   
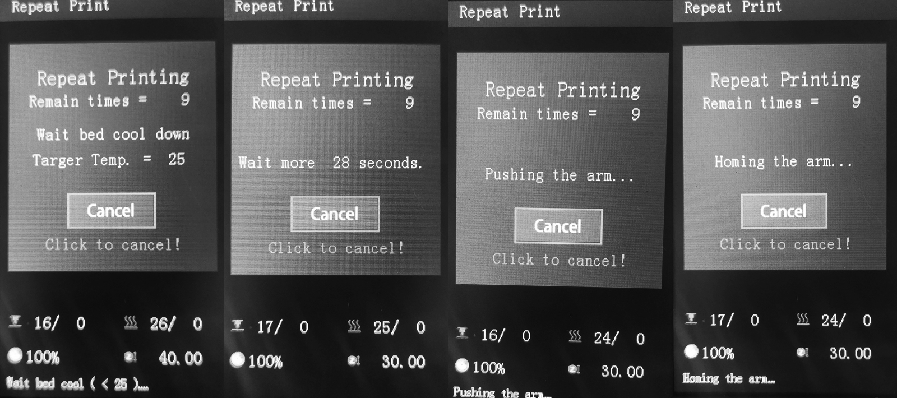
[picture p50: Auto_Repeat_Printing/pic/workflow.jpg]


### Description of settings:  
+ **Auto repeating**: Turn on/off the **Automatic Repeat Print** feature.  
+ **Repeat times:** Number of repeats, the actual printed number = Repeat times + 1.
+ **Push length:** Puhing-arm move forward length when removing the printed object. 
+ **Bed temp:** Wait the hotbed cool to this temperature before removing the printed object.
+ **Z Heigth:** Move Z-axis to this heigth before removing the printed object.  
+ **Base Heigth:** Heigth of the base. [**See advanced feature for details**][11]  

## 9. Apply Automatic Repeat Printing function   [return to contents>>][0]
There are two ways to apply the **Automatic Repeat Printing function**: ***Apply from LCD control panel*** or ***Apply by adding gcode***.    
### 9-1. Apply Automatic Printing function from LCD control panel.
+ Slice the 3d files to gcode file, which is the same as without **Automatic Repeat Printing** function.
+ Turn on the Repeat Printing and set parameters on the LCD screen.  
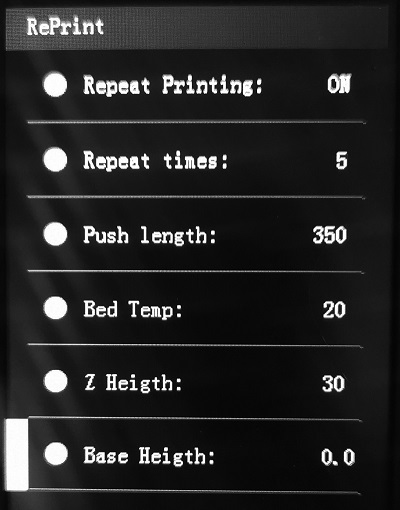
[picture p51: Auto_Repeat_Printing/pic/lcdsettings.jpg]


### 9-2. Apply Automatic Printing function by adding gcode.
You can also add the M182 command to the "Start G-code" of "machine setting" when slicing, detailed description of M182 command as below: 

    M182 Sx Nxx Zxx Txx Lxx

	//M182 command decscription
	M182: set Automatica Repeat Printing settings.  
	S[bool]: enable (= 1) or disable(= 0) auto repeat printing.  
	N[int]:  Repeat Printing times (1~999).  
	Z[int]:  Move Z axis to this heigth before pushing the arm.  
	T[int]:  Bed temperature (15~100).  
	L[int]:  Push arm length.  
	B[float]: Base heigth. (while used the print base)

	:memo:For example:
	 >>1. Need to print 10 pieces total. 
	 >>2. The hotbed temperature should be lower than 23℃ before removing. 
	 >>3. Move printing platform heigth to 65mm before removing.
	 >>4. Pushing the arm 350mm to remove the printed object.  
	you can add this command to the start G-code (before G28 command):
	M182 S1 N9 Z65 T23 L350 

## 10. Example Gcode files   [return to contents>>][0]
There are several testing gcode files in the [**Example**](./Example) directory:      

+ **Dummy.gcode**: This file is a "dummy" print file. It doesn't actually print anything, only help to test the repeat printing function quickly. You can download and copy this file to the SD card and followng the below steps to tes  *Automatic Repeat Printing* function:  
	+ **Step 1**. Turn on **Repeat Printing** and set the parameters on the LCD screen.
	+ **Step 2**. Start print *dummy.gcode* file from SD card, and watch the printer how to work.
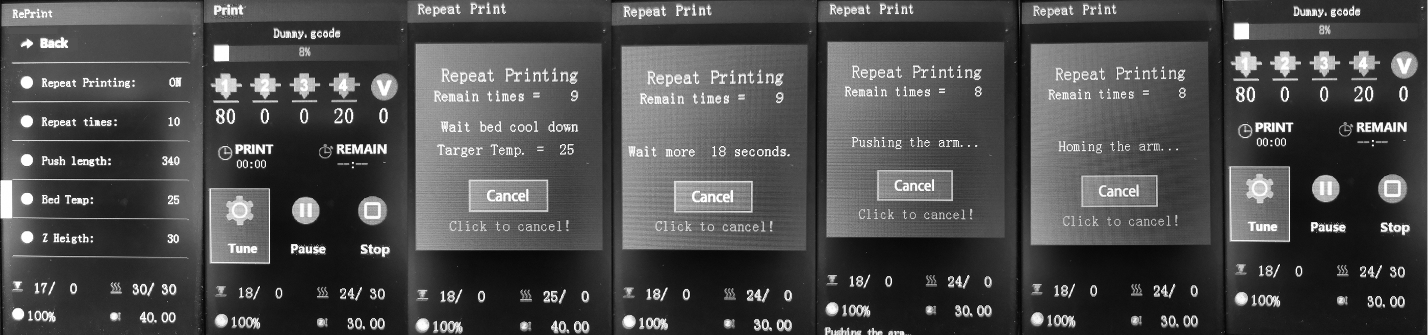
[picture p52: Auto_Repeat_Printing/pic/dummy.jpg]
   

+ **ShowHow.gcode**: This file is a "dummy" print file too, but a M182 command has been added in the "start Gcode" when slicing, you can download and copy the file to the SD card and print it and watch the printer how to work (don't need to set "Repeat Print" settings on LCD screen).
  
> **The below picture shows what's different between file "Dummy.gcode" with "ShowHow.gcode".**
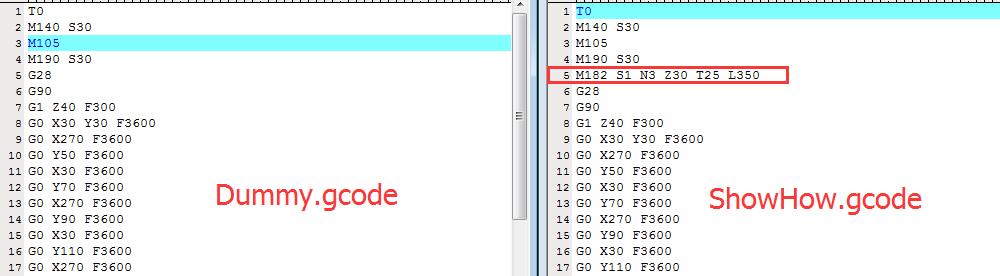
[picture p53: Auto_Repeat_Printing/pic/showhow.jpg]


+ **Demo.gcode**: This file is a "demo" print file. It print a small box with 30x30x50mm size. It can help you test the repeat printing function. the steps are as follows:  
	* **Step 1**. Turn off **Repeat repeating** on the LCD screen,
	* **Step 2**. Start print "Demo.gcode" file from SD card.
	* **Step 3**. Pay attention to adjust the heigth when printing first layer.
	* **Step 4**. Wait for printing finish.
	* **Step 5**. Wait the hotend cool down,  depending on the ambient temperature and it shoudl be lower than 25 degree.
	* **Step 6**.  Do **Prepare>>Move Axis>>Move Z** to move the Z axis to about 40mm.
	* **Step 7**.  Do **Control>>Repeat Print>>Push Arm Test** on the LCD MENU to push the arm and check if the printed object can be removed by the arm. 
If the above operation can successfully remove the printed object, you can start the repeat printing function on the LCD menu and test it.
+ **DemoRep.gcode**: This file is almost the same with **Demo.gcode**, but a M182 command is added in the "start G-code" while slicing, so you can print it directlly but don't need to turn on the "Repeat Printing" settings from LCD screen.

## 11. Advanced feature    [return to contents>>][0]
### 11-1. Print another gcode file
If you want to print another gcode file after finished, you can add an M183 command before the M182 command.    
> 
    M183 command description
    M183: Set the repeat printing file.  
    Example: M183 12345678.gco -> print file "12345678.gco"  

**:exclamation:Note:exclamation:The file name must be in 8.3 format and placed in the same directory with the previous file (it is recommended to place them in the root directory).**  
:memo:For example, you want to print 3d object "A" 7 copies and print 3d object "B" 3 copies, you need to:  
  
+ Add the below commands on the "start g-code" when slicing 3d model "A"
  
>
    M182 S1 N6 Zxx Txx Lxxx   
    M183 b.gco 
	;xx needs to be set as required 	

+ Add the below commands on the "start g-code" when slicing 3d model "B"

>    
    M182 S1 N2 Zxx Txx Lxxx  
	;xx needs to be set as required

+ Store the a.gco and b.gco to the same directory and print "a.gco" file first. 

<!-- ### 11-3. Add bed cooling FAN -->
<!-- :black_square_button: **TODO: To add an instruction about how to add the hot bed cooling fan.** -->
<!-- ### 11-2. Add print base -->
<!-- :black_square_button: **TODO: To add an instruction about how to add a base under the printed object.**   -->

[0]:https://github.com/ZONESTAR3D/Upgrade-kit-guide/tree/main/Auto_Repeat_Printing#contents
[1]:https://github.com/ZONESTAR3D/Upgrade-kit-guide/tree/main/Auto_Repeat_Printing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
[2]:https://github.com/ZONESTAR3D/Upgrade-kit-guide/tree/main/Auto_Repeat_Printing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
[3]:https://github.com/ZONESTAR3D/Upgrade-kit-guide/tree/main/Auto_Repeat_Printing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
[4]:https://github.com/ZONESTAR3D/Upgrade-kit-guide/tree/main/Auto_Repeat_Printing#4-wiring---return-to-contents  
[5]:https://github.com/ZONESTAR3D/Upgrade-kit-guide/tree/main/Auto_Repeat_Printing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  
[6]:https://github.com/ZONESTAR3D/Upgrade-kit-guide/tree/main/Auto_Repeat_Printing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
[7]:https://github.com/ZONESTAR3D/Upgrade-kit-guide/tree/main/Auto_Repeat_Printing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
[8]:https://github.com/ZONESTAR3D/Upgrade-kit-guide/tree/main/Auto_Repeat_Printing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 
[9]:https://github.com/ZONESTAR3D/Upgrade-kit-guide/tree/main/Auto_Repeat_Printing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
[10]:https://github.com/ZONESTAR3D/Upgrade-kit-guide/tree/main/Auto_Repeat_Printing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 
[11]:https://github.com/ZONESTAR3D/Upgrade-kit-guide/tree/main/Auto_Repeat_Printing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
[selllink]:https://www.aliexpress.com/item/1005003767078457.html
[PEIselllink]: https://www.aliexpress.com/item/1005004651715035.html

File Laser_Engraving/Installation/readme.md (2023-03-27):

## Installation and Wiring
### :one: Install the bracket to the laser engine
For Z9V5Pro, please install the bracket to the left side, for other printer, please install it to the center.     
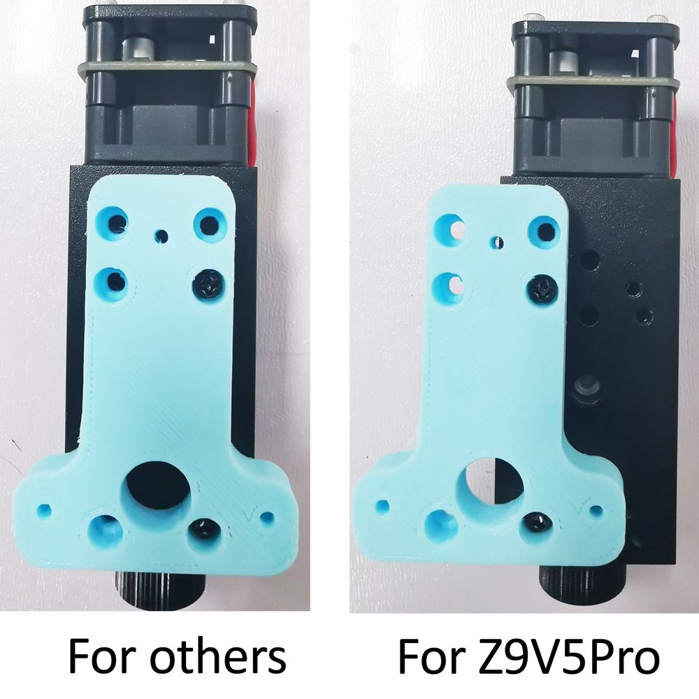
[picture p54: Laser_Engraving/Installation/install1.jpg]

### :two: Install the laser engine with bracket to the X carrier of the printer
For Z9V5Pro, please install the bracket to the left side, for other printer, please install it to the center.     
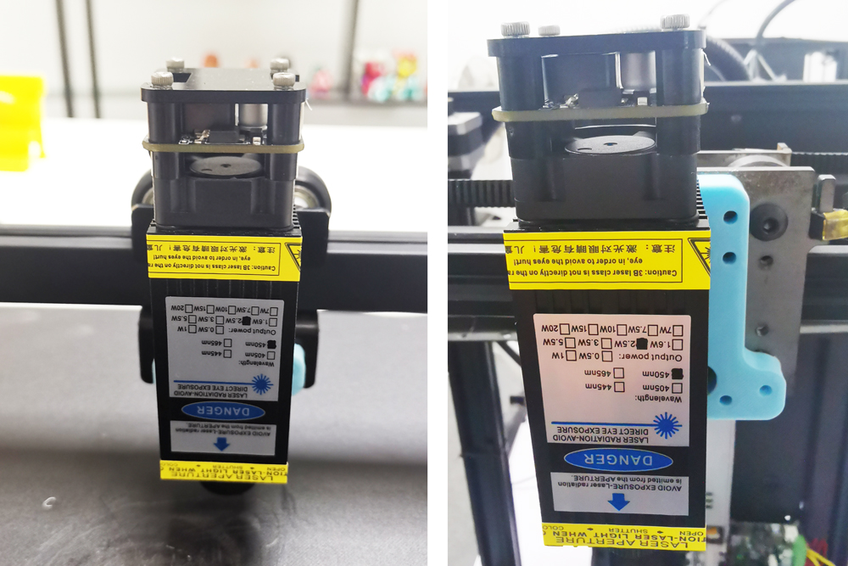
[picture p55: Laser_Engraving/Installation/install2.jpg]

### :three: Connect the laser engine to the controller board using the 3PIN cable.
:warning:Be careful not to invert the 2 ends of the wire (please refer to the color and terminal identification of the wire in the following picture).  
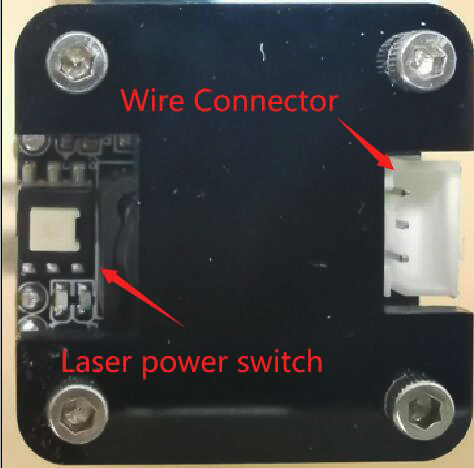
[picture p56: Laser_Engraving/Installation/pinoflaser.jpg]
      
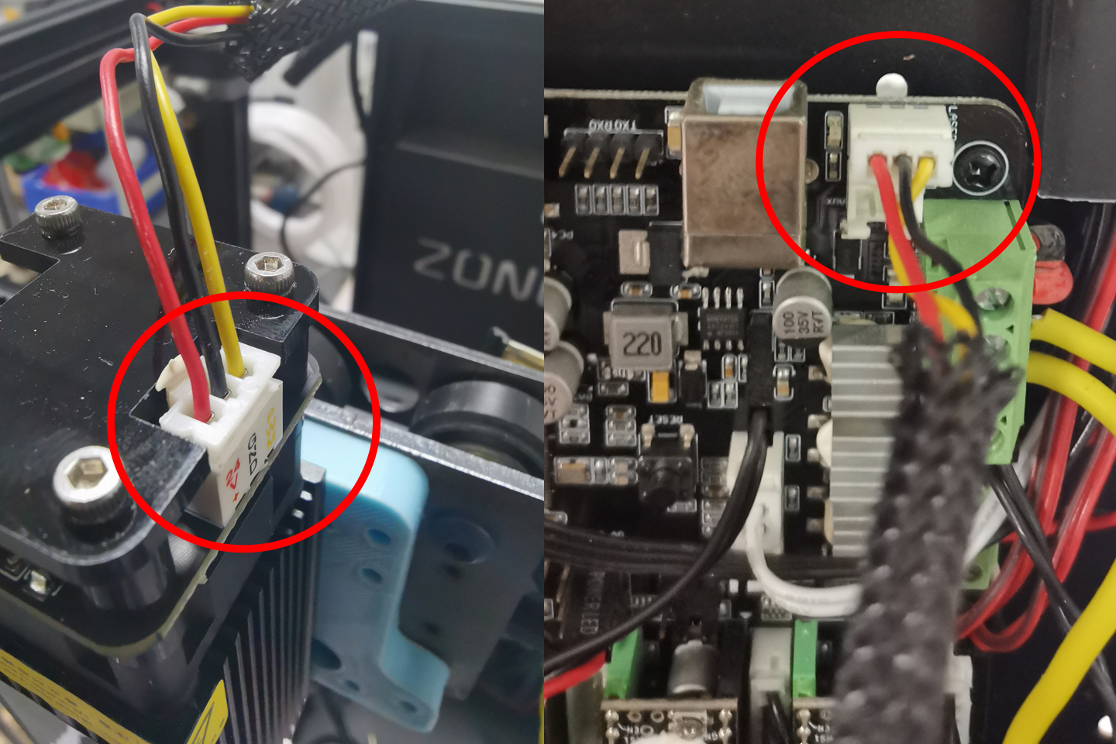
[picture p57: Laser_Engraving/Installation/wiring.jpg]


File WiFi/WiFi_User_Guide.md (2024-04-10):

# WiFi Feature User Guide
## Connect WiFi module
- Refer to the below picture to connect the WiFi module to the control board.
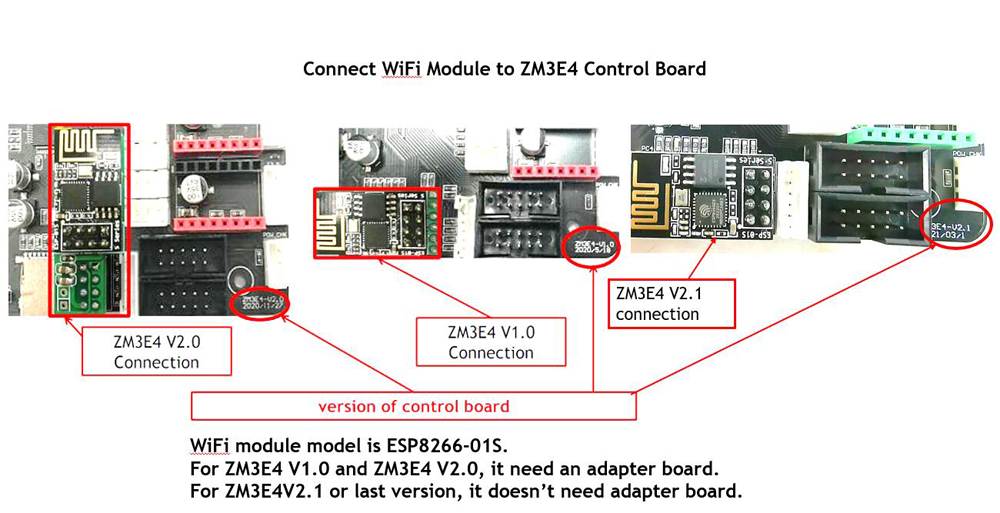
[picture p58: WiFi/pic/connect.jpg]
  
### :warning: Please check whether the version of the WiFi module and the version of the control board are paired correctly. If the control board is v2.0 but the WiFi module is v2.1 (without adapter), the printer cannot be powered on after the WiFi module is plugged in.

## Work Mode
The WiFi module can work in two modes, namely, **Access Point (AP)** mode or **Client Station** mode.
- **Access Point (AP) mode:** The control equipment (laptop, PC, mobile phone etc.) link to 3d printer directly. In Access Point mode, the access distance between the control equipment and 3d printer should be less than 5 meters. :star:**When the WiFi module leave factory, it works in this mode.** 
- **Client Station mode:** Both the control equipment and 3d printer link to router, transfer control command by router. In Cilent Station mode, you can operate the machine within the coverage of the router.
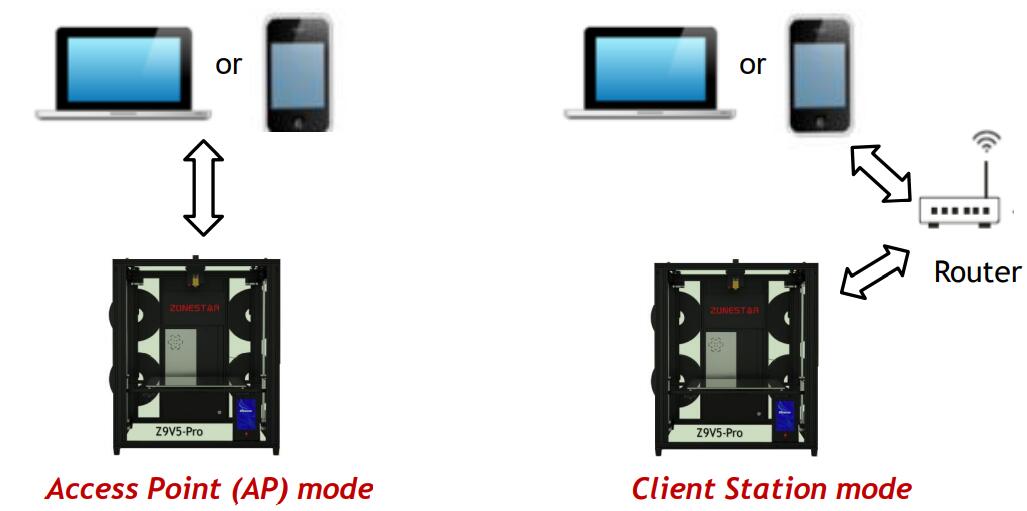
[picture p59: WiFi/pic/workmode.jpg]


### Video tutorial
(https://www.youtube.com/watch?v=ljA3FyNMTP4)

## Connet to printer by AP Mode
:warning: **You must use AP mode if you are connecting to the WiFi module for the first time.**  
:warning: **In AP mode, the distance between the printer and the control device should not exceed 5 meters.**   
1. Turn on the WiFi on LCD MENU “Control>>Configre>>WiFi”, after WiFi working, it will shows a IP address on the bottom of LCD screen “192.168.0.1”
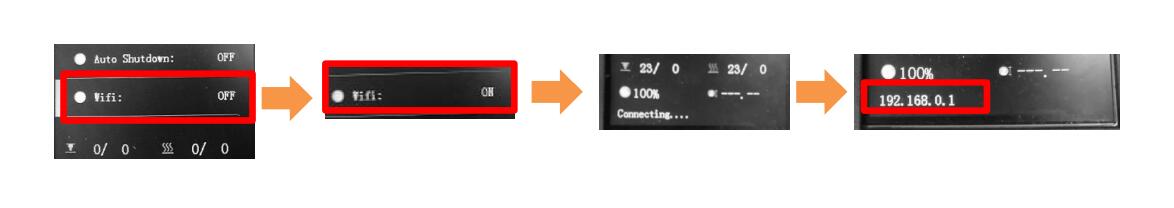
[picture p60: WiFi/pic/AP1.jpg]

2. Find the WiFi hotspot of **"ZONESTAR3D" or "ZONESTAR3DP"** on the PC or laptop (or any other device can receive the WiFi signal) and connect to this hotspot, <font size="6" color=#FF1111>password is 12345678</font>.  
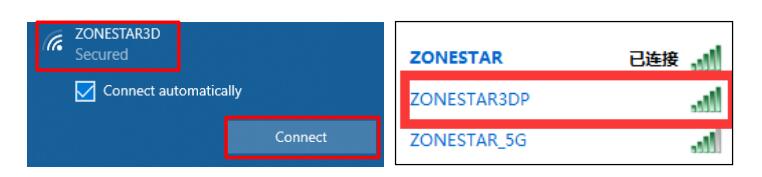
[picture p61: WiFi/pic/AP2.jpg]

3. Input IP address 192.168.0.1 in the web explorer and press "Enter" or "search", the web explorer will show the ESP3D console page.  
  
:star2: If a newer version of firmware is installed on your machine (Z9V5Pro and Z8PM4), a QR-code will be displayed on the LCD screen after the WiFi module is turned on successfully. If you use a mobile phone to control the 3D printer, you can directly scan the QR-code with the browser instead of typing "192.168.0.1"     
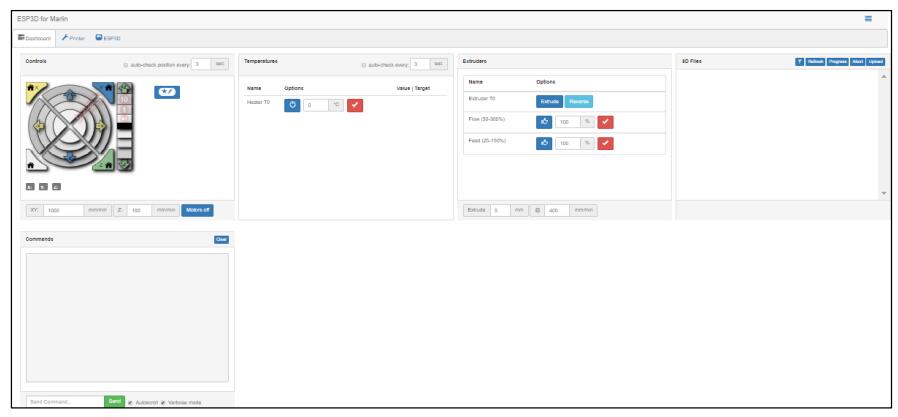
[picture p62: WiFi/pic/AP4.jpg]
  
4. You can control the 3d printer by ESP3D console page. For details, please refer to [ESP3D WebUI](https://github.com/luc-github/ESP3D-WEBUI)

## Switch to Client Station Mode from AP Mode
In the AP mode, your computer (mobile) is directly connected to the hotspot of the 3D printer, so you cannot access the internet through WiFi. If you have a wireless router and use WiFi to access the internet, you can switch to Client Station mode.
1. Refer to the following picture to set on **ESP3D console page**. 
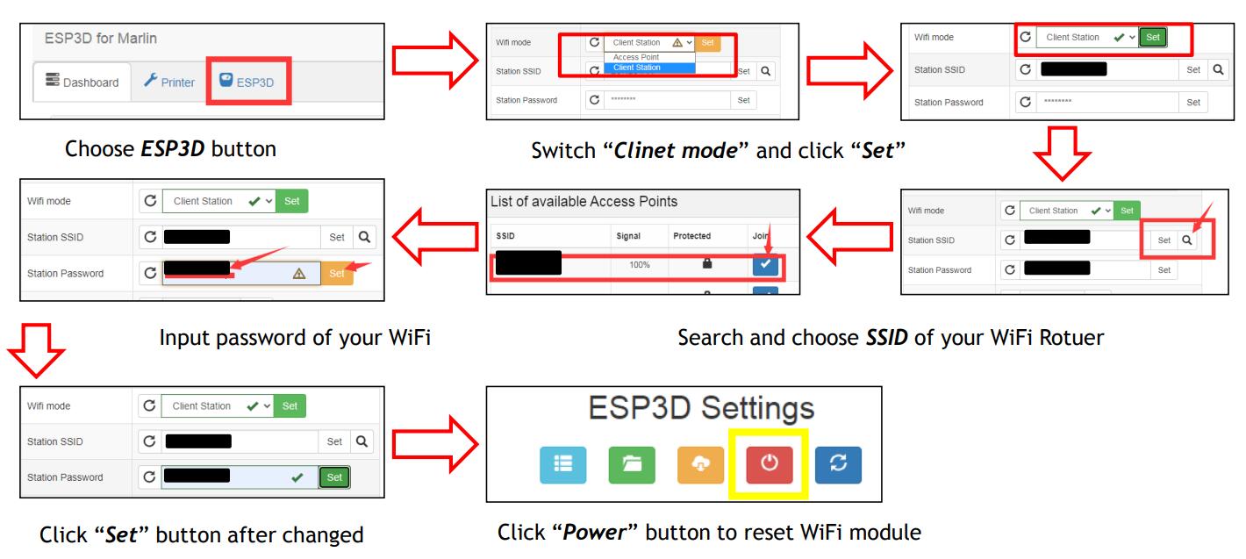
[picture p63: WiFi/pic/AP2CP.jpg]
    
**Station SSID      :**  the SSID of your WiFi hotspot.  
**Station Password  :**  the password of of WiFi hotspot.  
2. After reset the WiFi module, wait about 15 ~ 20 seconds, you can see the IP address on LCD screen as below.  
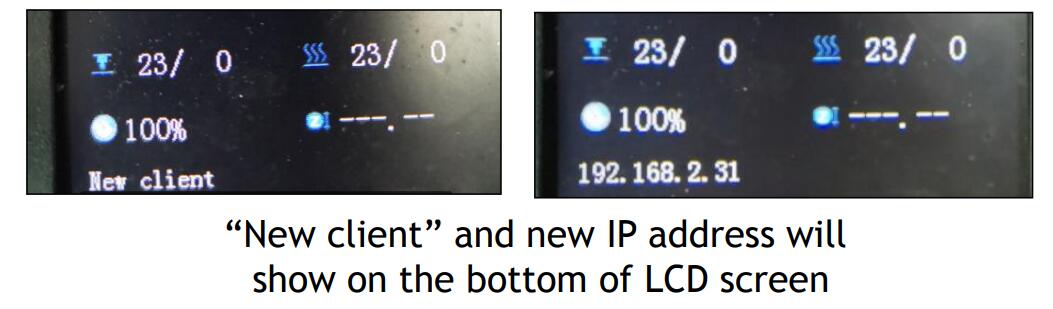
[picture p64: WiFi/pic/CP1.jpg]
  
3. Chaneg the WiFi hotspot to the SSID of your Rotuer on your PC or mobile phone.  
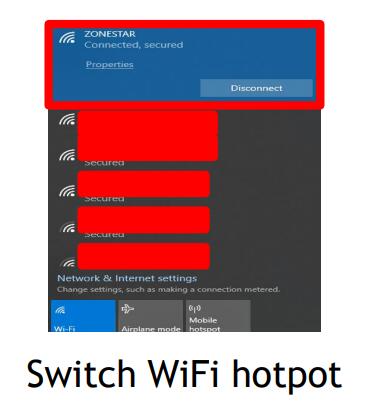
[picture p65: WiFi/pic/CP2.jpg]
  
4. Input the new IP address of your printer on the web explorer, the web explorer will show the ESP3D console page.      
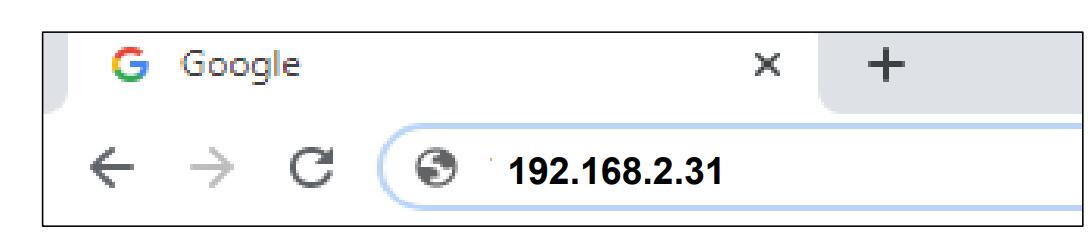
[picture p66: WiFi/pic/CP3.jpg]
  
:star2: If a newer version of firmware is installed on your machine (Z9V5Pro and Z8PM4), a QR-code will be displayed on the LCD screen after the WiFi module is reset successfully. If you use a mobile phone to control the 3D printer, you can directly scan the QR-code with the browser instead of typing the IP address.  

5. You can control the 3d printer by ESP3D console page. For details, please refer to [ESP3D WebUI](https://github.com/luc-github/ESP3D-WEBUI)

## Work on Client Station Mode
1. After switched to the client station mode, the WiFi module will save the SSID and password automatically. You only need to enter the IP address on web browser to access and control your 3D printer. 
2. The IP address of the 3D printer may be changed while the 3d printer is turned on. Please pay attention to the message on the LCD after the 3D printer is turned on.
3. If you forget or are not sure about the current IP address of the 3d printer, just need to turn off and then turn on WiFi feature on LCD screen and then find it on the LCD screen.

## Set WiFi Baud Rate
:warning: Upload gcode file to SD card via WiFi is slow, we suggest you copy the file directly if the gcode file is over 1M.  
You can improve the file uploading speed by modifying the baud rate of communication.   
:warning: You must set the same baud rate in the LCD display menu and ESP3D console page, otherwise you will not be able to control the 3D printer via WiFi.  
- **Step 1:** set the WiFi BaudRate on ESP3D console page and reset the WiFi module.
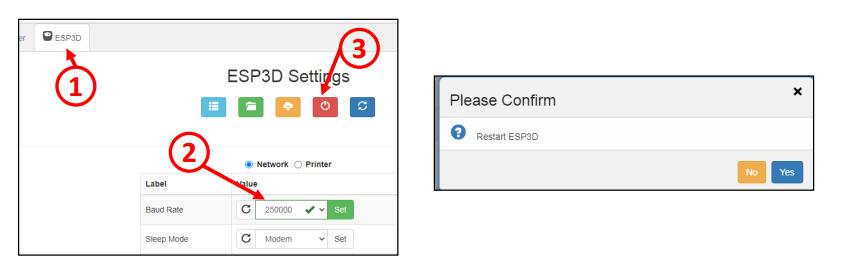
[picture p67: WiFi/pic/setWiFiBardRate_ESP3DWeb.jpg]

- **Step 2:** set the WiFi BaudRate on LCD menu.
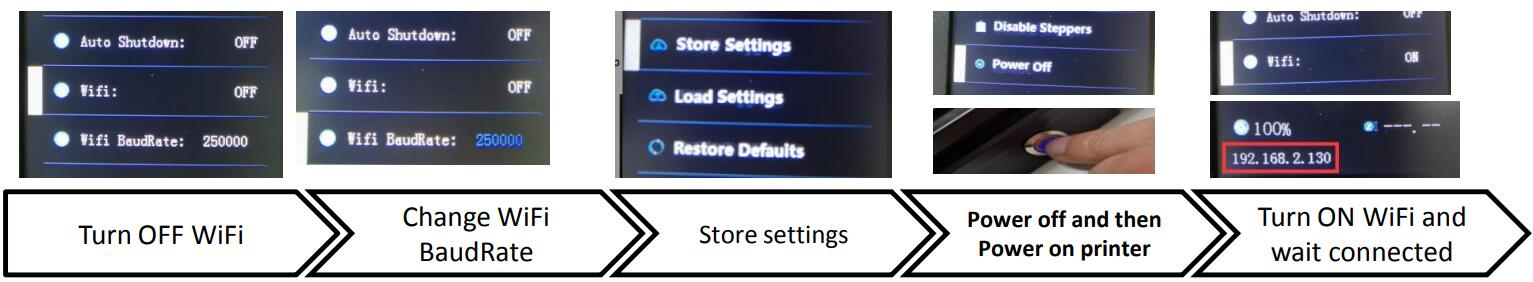
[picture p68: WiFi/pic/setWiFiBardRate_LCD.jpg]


## WebUI User Guide
The webUI of WiFi is base on ESP3D WebUI, for the detail user guide, please refer to [**ESP3D-WEBUI**](https://github.com/luc-github/ESP3D-WEBUI).

-----
### :orange_book: About Wiring of WiFi Module
#### Wiring For ZM3E4 Control board
- **For ZM3E4 V2.1 or newer board**: its WiFi connector are compatible with the ESP8266_01S WiFi module , you can plug the ESP8266_01S to the connector directly.    
- **For ZM3E4 V1/V2.0 board**: their WiFi connector are **not compatible** with the ESP8266_01S WiFi module, so we added a adapter board to the WiFi module, so you can purchase [**:gift:the ESP8266 WiFi module with adapter board**](https://www.aliexpress.com/item/1005002378551489.html) from our store.    
If you have a EPS8266_01S WiFi module without adapter, you can connect it to the ZM3E4V1/ZM3E4V2 with 6 PIN DuPont Wire (as below picture) to connect EPS8266_01S WiFi module with ZM3E4V1/ZM3E4V2.     
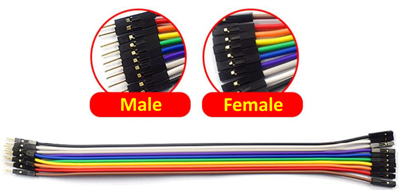
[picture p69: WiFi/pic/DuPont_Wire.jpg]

#### Pin define of ESP8266-S01 
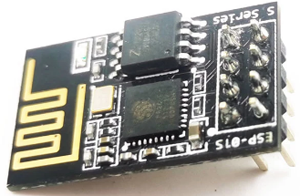
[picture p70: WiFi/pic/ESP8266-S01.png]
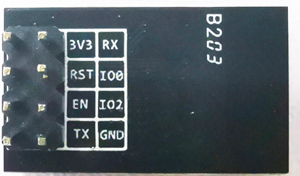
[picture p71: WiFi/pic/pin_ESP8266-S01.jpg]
 
#### WiFi connector Pin define of the ZM3E4V1
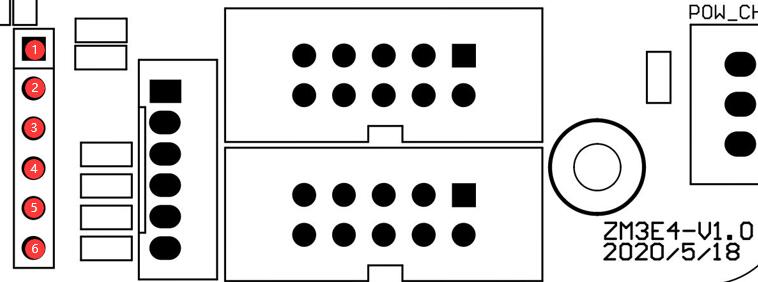
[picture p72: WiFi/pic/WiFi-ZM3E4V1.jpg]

#### WiFi connector Pin define of the ZM3E4V2.0
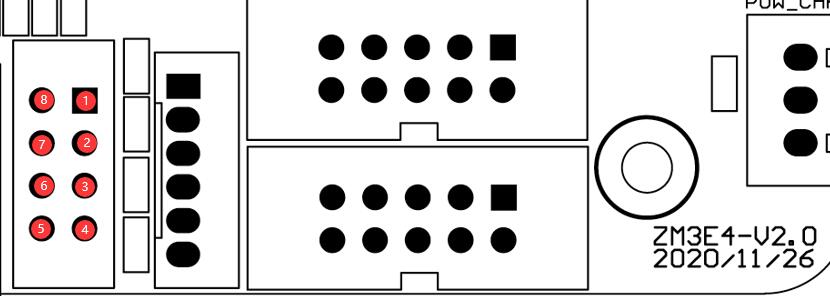
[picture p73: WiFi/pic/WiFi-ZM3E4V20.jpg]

#### Wiring
| pin of ESP8266  |  Description |  pin of ZM3E4V1 |pin of ZM3E4V2.0 | 
|---|---|---|---|
| 3V3 |  Power DC+ |  Pin 1 (+3.3V)  | Pin 5 (+3.3V) |
| RST |  Reset WiFi |  Pin 5 (W_RST)  | Pin 7 (W_RST) |
| EN |  Chip Enable |  Pin 6 (W_CS) | Pin 6 (W_CS)  |
| TX |  Data Transmit  |  Pin 3 (W_RX) | Pin 8 (W_RX)  |
| RX |  Data Received  |  Pin 4 (W_TX) | Pin 4 (W_TX)  |
| IO0 |  Not connect | | |
| IO1 |  Not connect | | |
| GND |  Power DC- |  Pin 2 (GND) | Pin 1 (GND) |
#### Wiring For ZM3E2 Control board
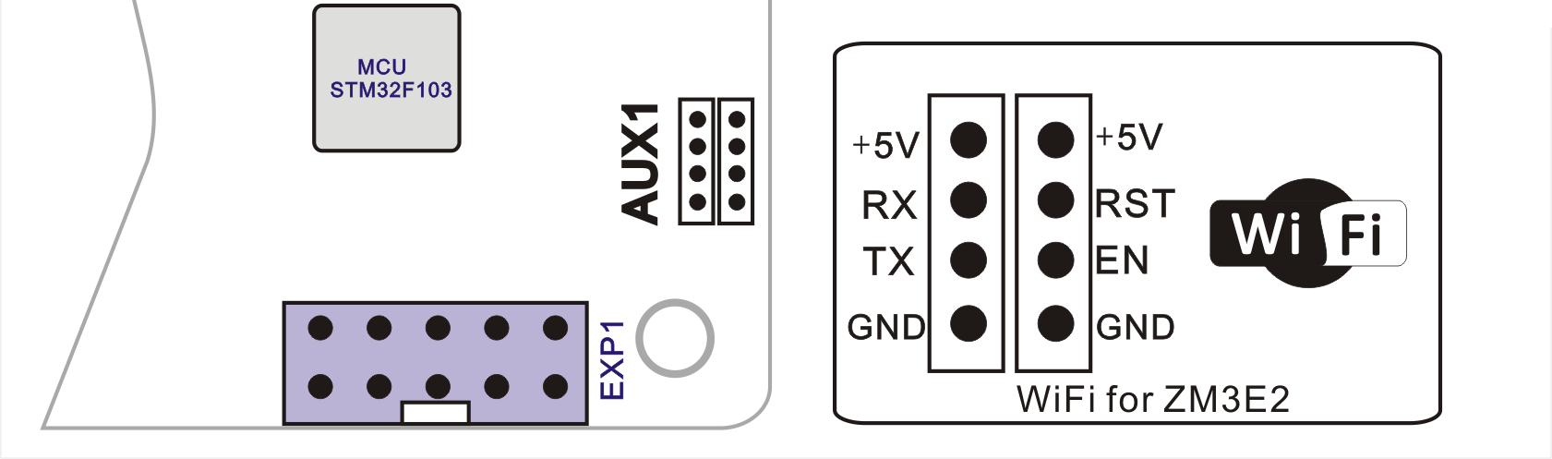
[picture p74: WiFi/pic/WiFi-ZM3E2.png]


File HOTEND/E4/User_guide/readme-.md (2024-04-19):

[PRUSA]: https://github.com/ZONESTAR3D/Slicing-Guide/tree/master/PrusaSlicer#6-slicing-muti-color-for-e4-hotend
[CURA]: https://github.com/ZONESTAR3D/Slicing-Guide/tree/master/cura
[S3D]: https://github.com/ZONESTAR3D/Slicing-Guide/tree/master/Simplify3D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
[ENDGCODE]: https://github.com/ZONESTAR3D/Slicing-Guide/blob/master/PrusaSlicer/Custom_Gcode.md#end-g-code
[STARTGCODE]: https://github.com/ZONESTAR3D/Slicing-Guide/blob/master/PrusaSlicer/Custom_Gcode.md#start-gcode
[FIRMWARE]: https://github.com/ZONESTAR3D/Firmware

----
## <a id="choose-language">:globe_with_meridians: Choose language </a>









<!-- [![](../../../lanpic/SA.png)](https://github.com/ZONESTAR3D/Upgrade-kit-guide/tree/main/HOTEND/E4/User_guide/readme-ar.md) -->

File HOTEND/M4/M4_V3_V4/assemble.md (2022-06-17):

## How to assemble / disassemble M4-V3(V4) hotend
### How to assemble M4 hotend
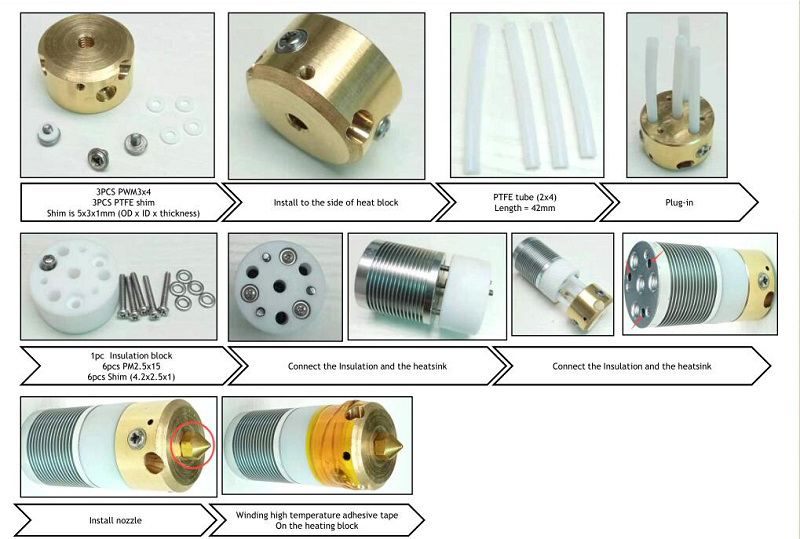
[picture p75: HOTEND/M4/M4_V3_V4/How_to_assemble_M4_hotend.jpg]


### How to assemble M4 printhead
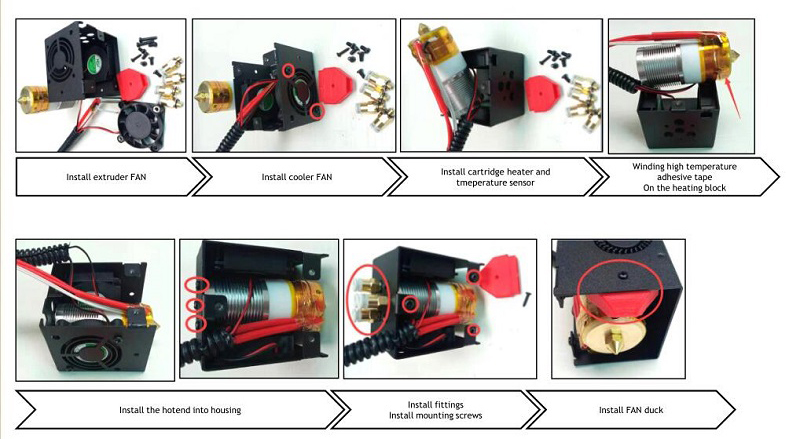
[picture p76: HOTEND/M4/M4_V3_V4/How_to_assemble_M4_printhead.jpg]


### How to disassemble M4 printhead
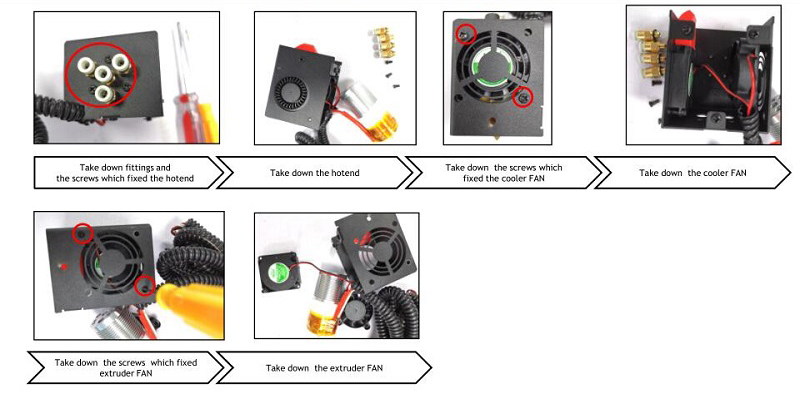
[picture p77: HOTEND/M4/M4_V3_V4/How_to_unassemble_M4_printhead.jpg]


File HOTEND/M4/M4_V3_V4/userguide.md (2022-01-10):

## User guide of M4-V3(V4) hotend
### 1. How to print singel color 3d object
+ Slicing a single color 3d mode file to gcode file.
+ Preheat the nozzle.
+ Use hotend clean tool to close the unused channle of hotend.
+ load filament to the hotend. **Recommend to load the filament to the center
channel.**
+ print gcode file from SD card.  
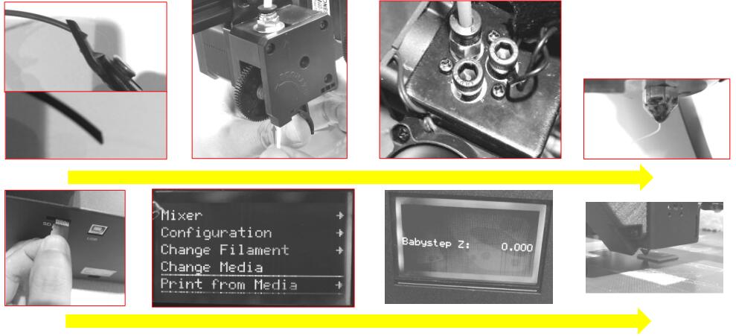
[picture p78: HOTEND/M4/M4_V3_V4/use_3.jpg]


### 2. How to change printed color by adjust mixing rate    
+ Start to print a singel color gcode file from SD card.
+ Wait until the print start to print, set on the LCD menu.  
#### For 128x64 dots LCD screen
+ **Tune>>Mixer>>Mix>>Component1~4(M4):** Arbitrarily adjust the percentage of extruder 1 ~ 4,the range is 0 ~ 100.  
+ **Tune>>Mixer>>Mix>>Comit V-tool Mix:** Redistribute the percentage of all extruders in proportion and send it to the current vtool.  
After setting up, on the ideal menu shows VTOOL:0 

#### For 4.3" TFT-LCD  
+ **Tune>>Mixer>>Current V-TOOL:** Set the vtool to 0.   
+ **Tune>>Mixer>>Mix>>Extruder1~4(M4):** Arbitrarily adjust the percentage of extruder 1 ~ 4, the range is 0 ~ 100.  
+ **Tune>>Mixer>>Mix>>Comit:** Redistribute the percentage of all extruders in proportion and send it to the current vtool. The current vtool value changes color.
After setting up, on the ideal menu shows Current VTOOL = 0


### 3. How to realize gradient printing

+ Start to print a singel color gcode file from SD card.  
+ Wait until the print start to print, set on the LCD menu.  
#### For 128x64 dots LCD screen
+ **Tune>>Mixer>>Gradient: disable>>**
	>
	> **Start Z:** set the start Z heigth(such as:0mm)  
	> **End Z:** set the END Z heigth(such as:200mm)  
	> **Start V-tool:** set the start V-tool(such as:0)   
	> **End V-tool:** set the end V-tool(such as:1)  
	After set Start Z isn’t equal to the End Z, and Start V-tool isn’t equal to End V-tool, the LCD will shows “Gradient : enable” and on the ideal menu shows gradient  

#### For 4.3" TFT-LCD
+ **Tune>>Mixer>>Gradient:OFF>>**
	>
	> **Start Z:** set the start Z heigth(such as:0mm)  
	> **End Z:** set the END Z heigth(such as:200mm)  
	> **Start V-tool:** set the start V-tool(such as:0)   
	> **End V-tool:** set the end V-tool(such as:1)  
	After set Start Z isn’t equal to the End Z, and Start V-tool isn’t equal to End V-tool, the LCD will shows “Gradient Mix Z:xxx->xxx V:xx->xx” and on the ideal menu shows gradient  


#### Realize gradient mixing by modifing gcode file
You can also add a M166 command into the "start G-code" of the machine setting when slicing, so it can automatically work when print from SD card.  
  
+ **To add a "M166" command, it can start a "Gradient Mixing".**
> 
	Descitpion of M166 command
	M166: Start a gradient mix  
	S[bool] - Enable / disable gradients
	A[float] - Starting Z for the gradient
	Z[float] - Ending Z for the gradient.
	I[index] - V-Tool to use as the starting mix.
	J[index] - V-Tool to use as the ending mix.
	For example: M166 S1 A0 Z200 I0 J1
	S1->Enable gradient mix 
	A0->startZ is 0mm 
	Z200-> EndZ is 200mm 
	I0 -> Start V-tool is 0 
	J1 -> End Vtool is 1

### 4. How to realize random printing

+ Start to print a singel color gcode file from SD card.  
+ Wait until the print start to print, set on the LCD menu. 
#### For 128x64 dots LCD screen
+ **Tune>>Mixer>>Random Mix: disable>>**
	>
	> **Start Z:** set the start Z heigth(such as:0mm) End Z: set the END Z heigth(such as:200mm)
	> **Height:** set interval distance(such as:10mm), When the z-axis distance changes beyond this value, the mixing ratio changes randomly once.
	> **Extruders:** set the number of extruders with random variation(such as:4)
	After set Start Z isn’t equal to the End Z, the LCD will shows “Gradient : enable” and on the ideal menu shows random.

#### For 4.3" TFT-LCD
+ **Tune>>Mixer>>Random Mix: OFF>>**
	> **Start Z:** set the start Z heigth(such as:0mm) End Z: set the end Z heigth(such as:200mm)
	> **Height:** set interval distance(such as:10mm), When the z-axis distance changes beyond this value, the mixing ratio changes randomly once.
	> **Extruders:** set the number of extruders with random variation(such as:4)
	After set Start Z isn’t equal to the End Z, the LCD will shows “Random : ON” and on the printing menu shows: "Random Mix Z:xx->xx H:xx.x E:xx


#### Realize Random mixing by modifing gcode file
You can also add a M167 command into the "start G-code" of the machine setting when slicing, so it can automatically work when print from SD card.  

+ **To add a "M167" command, it can start a "Random Mixing".**
> 
	Descitpion of M167 command.
	M167: Start a random mix.
	S[bool] - Enable / disable random mix.
	A[float] - Starting Z for the random.
	Z[float] - Ending Z for the random.
	H[float] - Minimum height of changing mixing rate.
	E[int] - how many extruders used on random mixing.
	For example: M167 S1 A0 Z100 H0.2 E3
	S1->Enable Random mix 
	A0->start Z heigth is 0mm 
	Z100->End Z heigth is 100mm 
	H0.2->change color every 0.2mm
	E3->3 extruders (Extruder#1 to Extruder#3) will be used

### 5. Hot to print multi-color 3d objects
+ [**Slicing guide**](https://github.com/ZONESTAR3D/Slicing-Guide)  
+ [**Example**](../Example/readme.md)

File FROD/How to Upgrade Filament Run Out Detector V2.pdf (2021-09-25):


# How to install and use Filament Run Out Detector Ver: 2.0

## For FROD V4

## Wiring


Refer to the wiring diagram in installation/user manual to connect the FROD.

For Z5/Z5X/Z6/Z8T， there is a 2-PIN connector with the extruder motor wire, it has a lable FROD,

connect this connector to the FROD (fig1)

For Z9, connect the 3PIN wire of FROD to the X+ connector of the control board(fig2).

fig1 | fig2

1. Let the filament throung to the FROD and enter the extrusion feeder (Fig 3).
2. Print from Sdcard, once filament rool is run out, printing will be paused, and filament will be returned from extrusion feeder automatically .
3. Pulled out filament from the extrusion feeder. Insert a new filament roll into the extrusion feeder until you can see it in the filament guide tube, press the button on control panel, printer will feed the filament into hotend automatically.
4. Note whether the filament is flowed out from the nozzle. If not, continue to feed the filament by executing “Extrude more” command on LCD MENU.
5. Use tweezers to remove filament from nozzle and then select “Resume print” to continue printing.


Fig 3


Fig 4

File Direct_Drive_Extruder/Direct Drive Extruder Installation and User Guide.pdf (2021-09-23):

# Direct Drive Extruder Installation and User Guide

## Ver: 1.0

## Installation


•1. Take down the orignal hotend from the x carrier

•2. Install the direct drive extruder (DDE ) to the same position of the carrier

Z9 print head | Z6 print head

Loosen or remove 3 screws to take down the hotend from X carrier

Install the DDE to the x carrier, note the Z6 and Z5X is different with other 3d printer model s

Fixing Screws for

Z5/Z8/Z9/Z10

Fixing screws for

Z6/Z5X

## Wiring


E0-MOT

E0-HEAT

E0TEMP
FAN (Extruder FAN)
FAN2 (HOTEND Cooling FAN)

Control board

## Wiring


You may need to change the stepper motor working direction, please refer to the below picture simply to exchange PIN1 and PIN3 of the motor cable, the motor working direction will be reversed:

### TIPS: Use a knife to turn up the clip of the terminal and then pull out the wiring

### exchange PIN1 and PIN3

## Set steps/mm parameter of extruder

You may need to change the steps/mm parameter of the extruder, there are two method to set the

steps/mm parameter:

NOTE: 400 steps / mm is for the driving circuit with micro step setting 16:1. if your motor drive

controllers are different, please set according to the following parameters:

E Steps/mm = 200 * microsteps / 8

### 1. Add “M92 E400” command in the “start gcode” of slicing software:

You can add a “M92 E400” command in the “start gcode” of slicing software, when printing from SD

card, it will change the steps/mm to 400.

PS: The parameter won’t be stored to the printer.

### 2. Set on LCD screen:

- For LCD128x64:

Configuration>>Advanced settings>>Steps/mm>>Estpe/mm: 400 (change to 400)

Configuration>>Store settings

- For LCDDWIN(4.3INCH-TFT):

Config>>Motion>>Steps/mm>>Steps/mm E:

Config>>Store settings

## Install the bed leveling sensor


PL | Bltouch(3DTouch) sensor -08N proximity sensor

## Slicing settings

Slice settings are usually related to the shape of the printed model, the filament type and the printer,

etc. The main parameter you need to pay attention to is about the retraction settings. The following

settings are for your reference:

Filament type | Retraction length | Retraction speed | Print speed
PLA/PLA+/PETG/ABS | 6~16mm | 20~30mm/s | 80 mm/s Max
Silk-PLA | 12~16mm | 25~30mm/s | 60 mm/s Max
TPU(95A) | 1~8mm | 20~30mm/s | 50 mm/s Max
TPU(87A) | 1~5mm | 0~20mm/s | 30 mm/s Max
TPU(83A) | 0~3mm | 0~10mm/s | 25mm/s Max

## NOTICE

For Z9V5, you may need to install the X ENDSTOP (that one on the FRONT-LEFT coner) from the bottom

to the TOP, please refero to the below picture


### Move the wire front Pull out the wire more

### Cut unused pin of limit switch


### Install the limit switch to the top

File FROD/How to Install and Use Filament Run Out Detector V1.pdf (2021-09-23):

# How to install and use Filament run out detector

### Ver: 1.0

1. Connect filament run out detector to E-SW connector or Z+ connector of control board according to wiring diagram in installation/user manual.
2. Preheat nozzle, and set temperature to 180~200 degrees.
3. Let filament through filament run out detector (for the direction of entry , please refer to the arrow on the detector), then insert filament into extrusion feeder and until filament reach the nozzle. Feed filament manually until you can see it is flowed out from nozzle steadily.
4. Print a gcode file from the SD card.


Note: If the filament run out detector doesn’t work, you need to check wiring or upgrade the firmware of control board.

1. Once filament is run out, printing will be paused, and filament will be returned from extrusion feeder automatically .
2. Waiting for the returning is finnished , and pulled out filament from the extrusion feeder. Insert a new filament roll into the extrusion feeder until you can see it in the filament guide tube, press the button on control panel, printer will feed the filament into HOTEND automatically.
3. Note whether the filament is flowed out from the nozzle. If not, continue to feed the filament by executing “Extrude more” command on LCD MENU.
4. Use tweezers to remove filament from nozzle and then select “Resume print” to continue printing.

## Operation


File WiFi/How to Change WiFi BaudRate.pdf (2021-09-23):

### How to Change WiFi BaudRate

you can change WiFi communication BaudRate to improve uploading file speed from WiFi.
Step 1: Change the BaudRate of the WiFi module in the ESP3D WebUI, and restart the ESP3D


Step 2: Modify the WiFi BaudRate on the LCD Menu(Menu>>Control>>Configre)


Turn OFF WiFi | Change WiFi


BaudRate | Store settings | Power off and then Power on printer


Turn ON WiFi and
wait connected

NOTE:
1. 921600 baud rate of WiFi module is not available at present, we will try to solve it

### 2. Higher baud rate will reduce the working distance of WiF

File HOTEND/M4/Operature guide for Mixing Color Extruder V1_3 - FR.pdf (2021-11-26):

# Guide d'utilisation pourextrudeuse de couleur de mélange

V1.3

## Pour la 4ème version M3 et M4 hotend

2

# Structure et principe de fonctionnement

## •Structure de mélange de couleur hot end

Raccords Pour fixer le tube PTFE sur la hotend; Dissipateur de chaleur Connectez le hotend à l'imprimante; Tube intérieur PTFE (tube Ø 4x2 PTFE); frais; Guide de filament (Tube Ø 4x2 PTFE); bloc calorifuge; Bloc chauffant Faire fondre et mélanger le filament; Buse MK7/MK8 type; Filament; Salle de mixage

garder le tube intérieur en PTFE au frais

Isolation de la gorge avec filament pour garder le filament au

Pour connecter le chargeur d'extrusion et la hotend

Pour isoler le bloc chauffant du dissipateur thermique

Un chauffe-cartouche de 50 W est utilisé pour le chauffage Une thermistance est utilisée pour mesurer la température

## •Principe de mélange des couleurs:

1. Les filaments fondent et se mélangent dans la salle de mélange, puis s'écoulent de la buse.
2. Pour changer le rapport d'alimentation, il peut obtenir un filament de couleur différente.

# !!ATTETION!!


## NE PAS charger/décharger le filament lorsque la température de la buse est inférieure à 150℃


N'introduisez PAS de filament de plus de 10 mm si l'un des canaux est vide, sinon cela pourrait le boucher. Vous pouvez:
1. Chargez le filament sur tous les canaux.

### 2. Utilisez un « outil de nettoyage hotend » pour

fermer les canaux vides.

# Comment imprimer un objet 3D monochrome

Étape 1 : reportez-vous au guide de silcing pour mélanger l'imprimante couleur pour convertir le fichier de mode 3D en fichier gcode.
Étape 2: préchauffer la buse à environ 170 degrés

Étape 3: Utilisez l'outil de nettoyage hotend pour fermer le canal inutilisé de hotend

Étape 4 : chargez le filament sur la hotend. REMARQUE : pour l'imprimante M4, il est recommandé de charger le filament au centreChannel, et utilisez "hotend clean tool" pour fermer les autres canaux.
Étape 5 : imprimer le fichier gcode à partir de la carte SD


## Changer la couleur d'impression en ajustant le taux de mélange (LCD12864)

Étape 1. Commencez à imprimer un fichier gcode couleur unique (Vase.gcode) à partir de
la carte SD.
Étape 2. Pour l'écran LCD12864, réglez sur le menu>>


●Mixer>>V-tool actif : sélectionnez le vtool actuellement imprimé ou utilisez la valeur par défaut,la plage est de 0 ~ 15.
●Mixer>>Mix>>Component1~3(4 for M4) : ajustez arbitrairement le pourcentage de l'extrudeur 1~3(4 for M4),la plage est de 0 ~ 100.
●Mixer>>Mix>>Comit V-tool Mix : redistribuez le pourcentage de tous les extrudeurs en proportionet l'envoyer au vtool actuel.

Après la configuration, sur le menu idéal affiche VTOOL:0

# Comment réaliser l'impression en dégradé (LCD12864)

Étape 1. Commencez à imprimer un fichier gcode couleur unique (Vase.gcode) à partir de la carte SD.
Étape 2. Pour l'écran LCD12864, réglez sur le menu>>


Mixer>>Gradient: disable
>> Start Z: définissez la hauteur de début Z (par exemple: 0 mm)

>> End Z : définissez la hauteur de FIN Z (par exemple : 200 mm)

>> Start V-tool: définissez le V-tool de début (par exemple : 0)

>> End V-tool : définissez le V-tool de fin (par exemple : 1)
Après avoir défini Start Z n'est pas égal à End Z, et Start V-tool n'est pas égal à End Vtool,l'écran LCD affichera « Gradient : enable » et sur le menu idéal affichera le dégradé

# Réalisez la couleur de mélange aléatoire(LCD12864)


Étape 1. Commencez à imprimer un fichier gcode couleur unique (Vase.gcode) à partir de la carte SD.
Étape 2. Pour l'écran LCD12864, réglez sur le menu>>

Mixer>>Random Mix: disable >>

>>Start Z: définissez la hauteur de début Z (par exemple: 0 mm)

>> End Z : définissez la hauteur de FIN Z (par exemple : 200 mm)
>> Height: définissez la distance d'intervalle (par exemple : 10 mm), lorsque la distance de l'axe z change au-delà de cette valeur, le rapport de mélange change de manière aléatoire une fois.

>> Extruders: définir le nombre d'extrudeuses avec une variation aléatoire (par exemple:3)

Une fois que le début Z défini n'est pas égal à la fin Z, l'écran LCD affiche “Random : enable”

et sur le menu idéal affiche aléatoire.


## Changer la couleur d'impression en ajustant le taux de mélange (LCD-DWIN)

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

Étape 2. Pour l'écran TFT, définissez-le dans le menu>>

●Mixer>>Current V-TOOL : sélectionnez le vtool actuellement imprimé ou utilisez la valeur par défaut, la plage est de 0 à 15.
●Mixer>>Mix>>Extruder1~3(4 for M4) : ajustez arbitrairement le pourcentage de l'extrudeur 1~3(4 for M4), la plage est de 0 ~ 100.
●Mixer>>Mix>>Comit V-tool : redistribuez le pourcentage de tous les extrudeurs en proportion et envoyez-le auvtool actuel. La valeur vtool actuelle change de couleur.

Après la configuration, entrez dans l'impression, sur le menu d'impression affiche : Mix 0


# Comment réaliser l'impression en dégradé (LCDDWIN)

Étape 1. Commencez à imprimer un fichier gcode à une seule couleur (Vase.gcode) à partir de la carte SD.

Étape 2. Pour l'écran LCD-DWIN, définissez-le dans le menu>>

Mixer>>Gradient: OFF >>

>> Start Z: définir la hauteur Z de départ(par exemple:0mm)

>> End Z: définir la hauteur END Z (par exemple:200mm)

>> Start V-tool: définir le démarrage V-tool(par exemple:0)

>> End V-tool: définir la fin de V-tool (par exemple:1)

Une fois que Start Z n'est pas égal à End Z et que Start V-tool n'est pas égal à End V-tool, l'écran LCD affiche “Gradient : ON” et sur le menu d'impression affiche: Gradient 0--->1


# Réalisez la couleur de mélange aléatoire (LCD-DWIN)

Étape 1. Commencez à imprimer un fichier gcode à une seule couleur (Vase.gcode) à partir de la carte SD.

Étape 2. Pour l'écran LCD-DWIN, définissez-le dans le menu>>

Mixer>>Random: OFF >>

>>Start Z: définissez la hauteur de début Z (par exemple: 0 mm)

>> End Z : définissez la hauteur de FIN Z (par exemple : 200 mm)
>> Height: définissez la distance d'intervalle (par exemple : 10 mm), lorsque la distance de l'axe z change au-delà de cette valeur, le rapport de mélange change de manière aléatoire une fois.

>> Extruders: définir le nombre d'extrudeuses avec une variation aléatoire (par exemple:3)
Une fois que Start Z n'est pas égal à End Z, l'écran LCD affichera “Random : ON” et sur le menu d'impression affiche: Random


# Comment imprimer un objet 3D multicolore

Étape 1 : Reportez-vous au "guide de silcing pour mélanger l'imprimante couleur" pour convertir le fichier de mode 3D en fichier gcode.
Étape 2: préchauffer la buse à environ 170 degrés et chargez le filament sur le hotend et utilisez l'outil de nettoyage du hotend pour fermer les canaux inutilisés
Étape 3: imprimer le fichier gcode à partir de la carte SD

TIPS 1:
Faire un repère sur le convoyeur d'extrusion afin de distinguer rapidement l'extrudeur
NOTE: Toutes les extrudeuses sont équivalentes et leur nombre dépend du câblage


TIPS 2: Canaux recommandés pour différentes quantités de filaments

TIPS 3:
Les étapes pour charger les filaments :


1. Chauffer la buse, puis utiliser l'outil de nettoyage hotend pour fermer le canal inutilisé (retirer d'abord les raccords) !
2. chargez tous les filaments dans le hotend, arrêtez-vous lorsqu'il entre dans le hotend d'environ 30 ~ 40 mm.
3. MENU>>Mouvement>>Déplacer l'axe>>Réglez V-TOOL sur 3 (pour M3) ou 4 (pour M4).
4. MENU>>Mouvement>>Déplacer l'axe>Extrudeuse>> alimenter jusqu'à ce que le filament s'écoule de la buse

# Comment imprimer un objet 3D multicolore

# À propos de la façon dont wo slicing, veuillez vous référer au guide dans ce lien: https://github.com/ZONESTAR3D/Slicing-Guide


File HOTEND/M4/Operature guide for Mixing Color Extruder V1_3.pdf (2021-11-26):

# Operation Guide for Mixing Color Extruder

V1.3

## For the 4

## th version M3 and M4 hotend

2

# Structure and Working principle

## •Structure of mixing color hot end

Fittings To fix the PTFE tube on the hotend; Heat sink Connect the hotend to the printer keep the inner PTFE tube is cool; Inner PTFE tube (Ø 4x2 PTFE tube); Filament guide(Ø 4x2 PTFE Tube); Heat-insulating block; Heating block To melt and mix the filament; Nozzle MK7/MK8 nozzle; Filament; Mixing Room

Isolation the throat with filament to keep the filament cool

To connect the extrusion feeder and hotend

To isolate the heating block from the heat sink

A 50W Cartridge Heater is used for heating A thermistor is used to measure temperature

## •Color mixing principle:

1. Filaments melt and mix in the mixing room, and then flow out from the nozzle.
2. To change the feed ratio, it can get different color filament.

# !!ATTETION!!


## DO NOT load / unload filament when the nozzle temperature is less than 150℃

DONOT feed-in filament over 10mm if any of the channels is empty, otherwise may cause it be clogged. You can:
1. Load filament to all channels.
2. Use a hotend clean tool to close empty channels.


# How to print single color 3d object


Step 1: Refer to the silcing guide for mixing color printer to covert the 3d mode file to gcode file.
Step 2: Preheat the nozzle to about 170 degree
Step 3: Use hotend clean tool to close the unused channle of hotend
Step 4: load filament to the hotend. NOTE: For M4 printer, recommend to load the filament to the center Channel, and use “hotend clean tool” to close the others channels.
Step 5: print gcode file from SD card

# Change print color by adjust mixing rate (LCD12864)

Step 1. Start to print a singel color gcode file(Vase.gcode) from SD card.


Step 2. For LCD12864 screen, set on the menu>>
●Mixer>>Active V-tool: Select the vtool currently printed, or use the default value,

the range is 0 ~ 15.
●Mixer>>Mix>>Component1~3(4 for M4): Arbitrarily adjust the percentage of extruder 1~3(4 for 4), range is 0 ~ 100.
●Mixer>>Mix>>Comit V-tool Mix: Redistribute the percentage of all extruders in proportion

and send it to the current vtool.

After setting up, on the ideal menu shows VTOOL:0

# How to realize gradient mix print (LCD12864)


Step 1. Start to print a singel color gcode file(Vase.gcode) from SD card.
Step 2. For LCD12864 screen, set on the menu>>

Mixer>>Gradient: disable >>

>> Start Z: set the start Z heigth (such as:0mm)

>> End Z: set the END Z heigth (such as:200mm)

>> Start V-tool: set the start V-tool (such as:0)

>> End V-tool: set the end V-tool (such as:1)
After set Start Z isn’t equal to the End Z, and Start V-tool isn’t equal to End V-tool, the LCD will shows “Gradient : enable” and on the ideal menu shows gradient


# How to realize random mix print (LCD12864)

Step 1. Start to print a singel color gcode file(Vase.gcode) from SD card.


Step 2. For LCD12864 screen, set on the LCD menu>>

Mixer>>Random Mix: disable >>

Start Z: set the start Z heigth(such as:0mm) End Z: set the END Z heigth(such as:200mm)


Height: set interval distance(such as:10mm), When the z-axis distance changes beyond

this value, the mixing ratio changes randomly once.

Extruders: set the number of extruders with random variation(such as:4)
After set Start Z isn’t equal to the End Z, the LCD will shows “Gradient : enable”

and on the ideal menu shows random


# Change print color by adjust mixing rate (LCD-DWIN)

Step 1. Start to print a singel color gcode file(Vase.gcode) from SD card.
Step 2. For TFT screen, set on the menu>>
●Mixer>>Current V-TOOL: Select the vtool currently printed, or use the default value, range is 0 ~ 15.

●Mixer>>Mix>>Extruder1~3(4 for M4): Arbitrarily adjust the percentage of extruder 1~4, range is 0 ~ 100.

●Mixer>>Mix>>Comit V-tool: Redistribute the percentage of all extruders in proportion and send it to the

current vtool. The current vtool value changes color.
After setting up, enter printing, on the printing menu shows: Mix 0


# How to realize gradient mixing print (LCD-DWIN)

Step 1. Start to print a singel color gcode file(Vase.gcode) from SD card.
Step 2. For LCD-DWIN screen, set on the menu>>

Mixer>>Gradient: OFF >>

>> Start Z: set the start Z height (such as:0mm)

>> End Z: set the END Z height (such as:200mm)

>> Start V-tool: set the start V-tool (such as:0)

>> End V-tool: set the end V-tool (such as:1)
After set Start Z isn’t equal to the End Z, and Start V-tool isn’t equal to End V-tool, the LCD will shows “Gradient : ON” and on the printing menu shows: Gradient 0--->1


# How to realize random mixing print (LCD-DWIN)

Step 1 Start to print a singel color gcode file(Vase.gcode) from SD card.
Step 2. For LCD-DWIN screen, set on the menu>>

Mixer>>Random: OFF >>

>> Start Z: set the start Z height (such as:0mm)

>> End Z: set the end Z height (such as:200mm)

>>Height: set interval distance (such as:10mm), When the z-axis distance changes beyond this value, the mixing

ratio changes randomly once.
Extruders: set the number of extruders with random variation (such as:4)
After set Start Z isn’t equal to the End Z, the LCD will shows “Random : ON” and on the printing menu shows:

Random


# How to realize gradient Random mixing by modifing Add gcode)

You can also add a M166/M167 command into the gcode file to apply gradient / random mixing printing, so it can

automatically work when print from SD card.

Gradient Mixing:
For example: M166 S1 A0 Z200 I0 J1
S1→Enable gradient mix A0 → startZ is 0mm Z200 → EndZ is 200mm I0 → Start V-tool is 0 J1 → End Vtool is 1

Random Mixing:
For example: M167 S1 A0 Z100 H0.2 E3
S1→Enable Random mix A0 → startZ is 0mm Z100 → EndZ is 100mm H0.2 → change color every 0.2mm height
E3 → 3 extruders (E0~E2) will be used to mix

Please note that there is no Tn(T0 ~ T16) command after M166/M167 command in the gcode code, because it will stop automatic gradient/Random mixing function

/**
* M167: Start a random mixing
* S[bool] - Enable / disable random mixing
* A[float] - Starting Z for the random mixing
* Z[float] - Ending Z for the random mixing
* H[float] - Minimum height of changing mixing rate * E[int] - how many extruders used on random mixing * */

/**
* M166: Start a gradient mix
*
* S[bool] - Enable / disable gradients
* A[float] - Starting Z for the gradient
* Z[float] - Ending Z for the gradient.
* I[index] - V-Tool to use as the starting mix. * J[index] - V-Tool to use as the ending mix. **/

# How to print multi-color 3d object

Step 1: Refer to the silcing guide for mixing color printer to covert the 3d mode file to gcode file.
Step 2: Preheat the nozzle to about 170 degree
Step 3: Load filament to the hotend, and use hotend clean tool to close the unused channles
Step 4: print gcode file from SD card(4C_Niko_Dog.gcode)

TIPS 1:
Make a mark on the extrusion feeder in order to quickly distinguish the extruder
PS: Their sequence depends on wiring


TIPS 2: Recommended channels for different quantities of filaments

TIPS 3:
The steps to load filaments:


1. Heat nozzle, and then use hotend clean tool to close unused channel (remove the fittings first)!
2. load all of the filaments into the hotend, stop when it enter the hotend about 30~40mm.
3. MENU>>Motion>>Move axis>>Set V-TOOL to 3(for M3) or 4(for M4).
4. MENU>>Motion>>Move axis>Extruder>> feed until the filament flow from the nozzle

# How to slicing multi-color 3d object

# About how wo slicing, please refer to the guide in this link: https://github.com/ZONESTAR3D/Slicing-Guide


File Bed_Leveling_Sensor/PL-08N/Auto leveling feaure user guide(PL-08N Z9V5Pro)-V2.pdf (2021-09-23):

# Auto leveling feaure user guide

# (Z9V5Pro)

## Bed Leveling Sensor: PL-08N

## Firmware Version V1.0.9 or last

## Note: If the hot bed is enough level without auto leveling, don’t use bed auto leveling feature, Bed automatic leveling will slightly reduce the printing

quality and increase the printing time.

# Prepare

Adjust the hotbed adjusting screws on the Z carrier, height is about 10mm

10mm


Set the HOME Z OFFSET, MENU>>Config>>Configure>>HOME Z Offset: x.xx


For SuperGlass, set to 3.5mm
Speical hotbed sticker, set to 0.4mm
Magnetic hotbed sticker: set to 1.0 mm

!ATTENTION!
HOME Z OFFSET is tell the printer the distance between the actual printing plane and the sensing plane. If you use different sensors and hotbed materials, you need to set this value. For example, if you use bltouch or zltouch, you need to set it to 0
PS: do “Config>>Store settings” to store it after changed it.

1. Make sure the hotbed and nozzle are cool, clean the filament on the nozzle.
2. Turn on the 3d printer.
3. Do Prepare>> Bed Leveling>> Point1~4.

## 4. Adjust the screws under the hotend, let the nozzle almost to touch the hotend

in the four corners.

# Level Corners


## NOTE: If you moved the position the nozzle or Z ENDSTOP, you need to do this

step again.

## After level coners, please try to print ”level_test_310.gcode” from SD card, and

check if the hotbed is enough level.

# Print test file

Press the knob twice within one second to open the babysteps menu, and then rotate the knob to fine tune the distance from nozzle to hotbed.

## NOTICE: if the hot bed is enough level, Don’t need to use bed auto leveling feature. You can ignore the below steps and start to print

## Step 1. Do Control>> Configure>> Auto Leveling(From OFF to ON) to turn on “Auto leveling” menu


# Auto Leveling >>> Catch Z offset

Step 2. Do Prepare>> Bed Leveling>>Catch Z-Offset.

## PS: if the HOME Z OFFSET is over(>=) 2mm, it will remind to remove the glass first. If you doesn’t use a glass bed, please check the settings of

HOME Z OFFSET.

# Auto Leveling >>> Leveling measure

Step 3. Do Prepare>> Bed Leveling>>Auto Leveling.

After measure done, the state of Auto leveling on Leveling menu will change from Unactived to Actived.


1. The measurement result should be between -1.0 to 1.0 mm. If it exceeds, it is recommended that you try to fine tune the printer or improve the flatness of the hotbed, because it may affect the printing quality.
2. If it is found that there is a large deviation in data arrangement between the Left/Right sides or the Front/Back sides, please adjust the bottom screw of the hotbed (when the data is + turn down the hotbed, when the data is - turn up the hotbed).

# Active auto leveling after printer reset


## Step 5. Do Prepare>> Bed Leveling>>Active Autolevel


## Once power off, the bed autolevel feature will auto unactive, you need to turn on it

on LCD menu.

## Step 4. Print the test file again refer to the page 4

# Supplement

probe Z offset; Probe Nozzle

## - What is “Probe Z offset ”and “HOME Z offset”

“probe Z offset”: it means the distace from the nozzle to the the sensing plane while the probe is triggered. “Catch Z Offset” function will get an average of “probe Z offset” automatically. We MUST manual level the bed by using “Point1~ Point4” before doing “Catch Z Offset”, otherwise the printer can’t get “probe Z offset” correctly.

the sensable plane

## - How to correct “Probe Z offset ” and “HOME Z offset”

For various reasons, the settings of “home Z offset” and “probe Z offset” may not be accurate, so you can manually adjust them to be more accurate.
1. When doing > > bed leveling > > auto leveling,
- if most of the obtained data showed in the table are shifted to the Positive, you can decrease the “Probe Z offset” and do "auto leveling" again ,
- if most of the obtained data showed in the table are shifted to the Negative, you can increase the “probe Z offset” and do auto leveling again.
PS: Ignore the datas at the 4 corners, it will be optimized in the firmware.
2. If you find that the nozzle is too close / far away from the printing plane when printing the first layer, you can incease / decrease home Z offset then print it again.

“HOME Z OFFSET”: For PL-08N bed auto leveling sensor, because it only can sensing a metal object, so “the sensing plane” is the surface of aluminum heatbed, but not the glass. We need to tell the printer the distance from the “real printing plane” to “the sensing plane”, that’s why we need to set the “HOME Z OFFST” to 3.5mm for a glass print plane like Z9V5Pro. By the same token, if we use a magnetic hot bed stickers, we must set “HOME Z OFFST” to 0.8mm ~ 1mm.

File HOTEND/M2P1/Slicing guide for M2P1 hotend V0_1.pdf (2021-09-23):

# Slicing guide for M2P1 Hotend

V0.1

# (Base on Cura 4.7 or later)

## Contents

•Connect the extrider motors with hotend

•Download and install Cura

•Import Zonestar Printer Settings

•Setting up printer

•Setting up filament

•Slicing singel color 3d object

•Slicing mullti colors 3d object

NOTE: For R series printers, due to the existence of multiple nozzles, the mechanical leveling step before printing is very important. Otherwise, if the nozzles are not at the same height, the nozzles will spray to the printing model during the printing process, which will lead to printing difficulties or no printing at all.

## Connect extruder motors with hotend

There are 3 input channels and two nozzles on the M2P1 hotend, please refer to the below drawing to connect the extrude Engine with the hotend.

Black: Fitting (Filament in); Red: Nozzle (Filament out); Extrude Engine; HOTEND; Channel 2; Channel 1; Channel 3

## Download and Install Cura

●Download cura from the below link and install it to your PC: https://ultimaker.com/software/ultimaker-cura
●About how to install and use Cura, please refer to this link: https://support.ultimaker.com/hc/en-us/categories/360002327600
●If you want to know more about the settings of cura, please install a “settings guide” plugin in cura, and then open it to study:


## Import ZONESTAR printer settings

1. Download "zonestar Cura Resources “ from the below link:
Download link: https://github.com/ZONESTAR3D/Document (https://github.com/ZONESTAR3D/Slicing-Guide)- (https://github.com/ZONESTAR3D/Slicing-Guide)and (https://github.com/ZONESTAR3D/Slicing-Guide)- (https://github.com/ZONESTAR3D/Slicing-Guide)User (https://github.com/ZONESTAR3D/Slicing-Guide)-Guide/blob/master/readme.md (https://github.com/ZONESTAR3D/Slicing-Guide)
2. Copy the contents of this sirctory to the installation directory of Cura
3. Run the cura


## Setting up printer


1: Open “Manage printers” | 2: Click “Add”
3: Select your printer model,then click “Add” | 4: Click “Activate”

## Setting up printer

Click “Machine settings”. Check the printer parameters.


Change the print size
if your printer is
different

## Set Nozzle offset


You may need to set the nozzle offset because the hotend may be rotated when installed.

2

1

3

Offset X: -6.71
Offset Y: -3.88

Offset X: 0
Offset Y: -7.75

Nozzle 1

If nozzle 2 at here

If nozzle 2 at here

## Setting up filament


In order to easy to view when slicing, you can define the filament color
1: Open “Manage materials...” | 2: Click “Create”

3:Find custom and modify relevant parameters in the information column on the right

4:Click “Duplicate”,and define more colors.

## Setting up filament

Select the filament color


You can choose ZONESTAR filament too, we have set some color for PLA and PETG

## Parameter setting of Extruder


In addition to the actual extruder, five virtual extruders are set in the machine settings. Virtual extruder refers to mixing the filament of extruder 1 and 2 to get a new color filament.
You can modify the mix rate if need, for example:
M163 S3 P0
M163 S2 P0
M163 S1 P10
M163 S0 P90
M164 S3
T3

; M163 command set the ratio of extruder

;M164 command set these ratio to the Extruder 3
;switch the current Extruder #3 (Apply the mix ratio to extrude motor)

## Slicing

As an example, we will use the same 3d object in the following pages. This 3d object is a 4-color model, which has already divided into four parts


NOTE: If you need to print multicolor, you need a 3d object that has been divided (the number of divided parts is according to the number of colors), and their origin position must be consistent in order to be merged.

## Load filament for printing 1 color 3d object

Load filament from extruder engine #3 and load filament into that independent channel

Black: Fitting (Filament in); Red: Nozzle (Filament out); Extrude Engine; HOTEND; Channel 2; Channel 1; Channel 3

## Slicing steps for 1 color 3d object


Load files | Merge Right click the mouse
Setlect all models

Set slicing parameter
(2)
save it | Copy the gcode file to SD card, then print it

Move/Scale/Rotate
the model

Slicing it

NOTE2: load “ZZM2P1_1C_Niko_Dog.3mf” to see the slicing settings

Assign extruder 3
to print (1)

NOTE1: use a separate
channel to print single color

Pass these two steps if the stl file is one color

## Settings for Slicing 1 color 3d object


## Use water-soluble materials

Some models need support to print well, you can load main filament (PLA/ABS) in to channel #3 and support filament (PVA/HIPS) into Channel #1, and closed Channel #2.

Black: Fitting (Filament in); Red: Nozzle (Filament out); Extrude Engine; HOTEND; Close this channel by using; A “hotend clean tool”; PLA; PVA; Channel 2; Channel 1; Channel 3

Load files; Set slicing parameter (2); Move/Scale/Rotate the model; Slicing it; Assign to extruder 3; Pre-View

## Slicing steps for 1 color 3d object + support

save it

Copy the gcode file to SD card and print it

Example: ZM2P1_frog

## Settings for Slicing 1 color 3d object


## Load filament for 2 colors 3d object – mode 1

You can use two independent nozzles to print two colors, and use oozing shield to deal

with oozing issue; Black: Fitting (Filament in); Red: Nozzle (Filament out); Channel 2; Channel 1; Channel 3; Close this channel by using; A “hotend clean tool”

## Slicing 2 colors 3d object (model 1)


## Settings for Slicing 2 colors 3d object

## Load filament for 2 colors 3d object – mode 2

You can also use the mixing color channels to print two color 3d object, there is only one nozzle so that there will be no oozing issue, but you need to set a color switch tower, it will take more time and filament.

Black: Fitting (Filament in); Red: Nozzle (Filament out); Channel 2; Channel 1; Channel 3

## Slicing 2 colors 3d object - model 2

Load files; Right click the mouse; Setlect all models; Right click the part and assign extruder for each

## Settings for Slicing 2 colors 3d object – mode 2


## Load filament for 3~8 colors 3d object

## Slicing 3 colors 3d object

## Slicing 4~8 colors 3d object

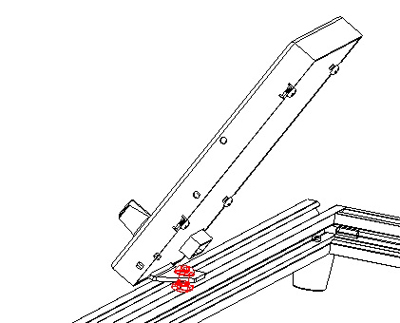
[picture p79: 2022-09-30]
TFT-LCD/LCD-DWIN/pictures/assembly-2.jpg

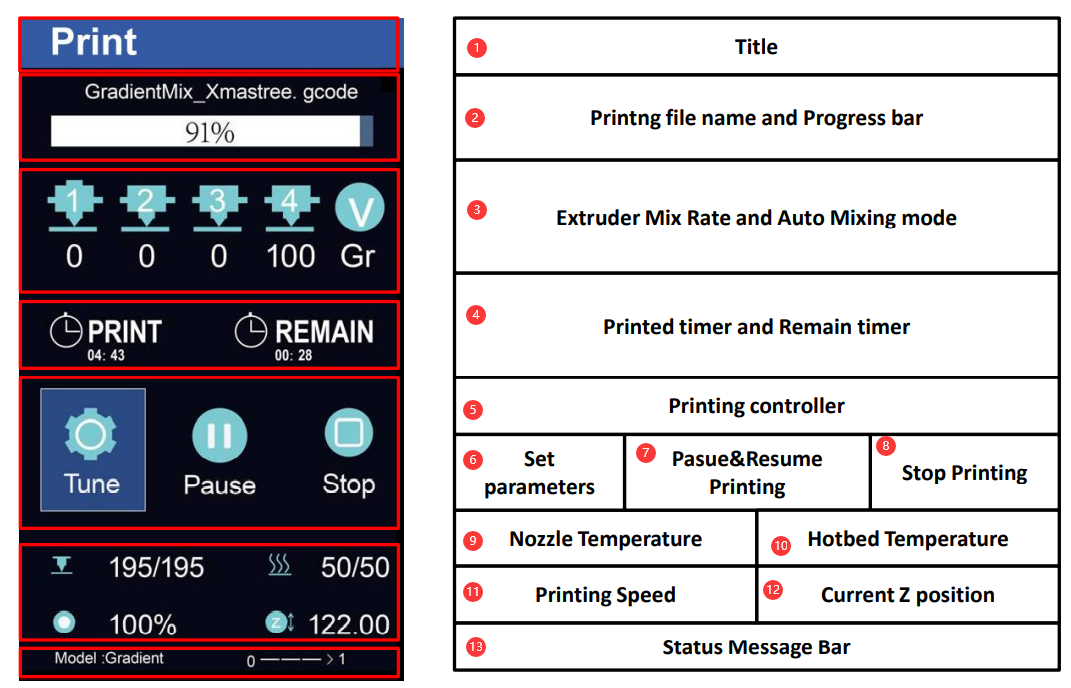
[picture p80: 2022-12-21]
TFT-LCD/LCD-DWIN/user_guide/pic/3.png

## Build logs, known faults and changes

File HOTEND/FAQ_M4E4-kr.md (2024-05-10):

[E4_STARTGCODE]: https://github.com/ZONESTAR3D/Slicing-Guide/blob/master/PrusaSlicer/Custom_Gcode.md#start-g-code
[M4_MIXMULTICOLORPRINT]: https://github.com/ZONESTAR3D/Slicing-Guide/blob/master/PrusaSlicer/PrusaSlicerGuide_M4.md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
[E4_TOOLCHANGE]: https://github.com/ZONESTAR3D/Slicing-Guide/blob/master/PrusaSlicer/Custom_Gcode.md#tool-change-g-code
[FW_Z9V5]: https://github.com/ZONESTAR3D/Firmware/tree/master/Z9/Z9V5/bin
[FW_Z9M4]: https://github.com/ZONESTAR3D/Firmware/tree/master/Z9/Z9M4
[FW_Z8P]: https://github.com/ZONESTAR3D/Firmware/tree/master/Z8/Z8P

----
## <a id="choose-language">:globe_with_meridians: Choose language </a>









<!-- [![](../lanpic/SA.png)](https://github.com/ZONESTAR3D/Upgrade-kit-guide/tree/main/HOTEND/FAQ_M4E4-ar.md) -->

----
# E4 및 M4 핫엔드에 대한 FAQ
- [**E4와 M4 핫엔드의 차이점은 무엇인가요?**](#A1)
- [**어떤 종류의 핫엔드를 선택해야 하나요?**](#a2)
- [**핫엔드에 필라멘트를 올바르게 로드하는 방법은 무엇입니까?**](#a3)
- [**M4 핫엔드와 E4 핫엔드의 슬라이싱 설정 차이점은 무엇입니까**](#a4)
- [**M4와 E4 핫엔드 간에 어떻게 전환합니까?**](#a5)

-----
## <a id="a1">E4와 M4 핫엔드의 차이점은 무엇인가요?</a>
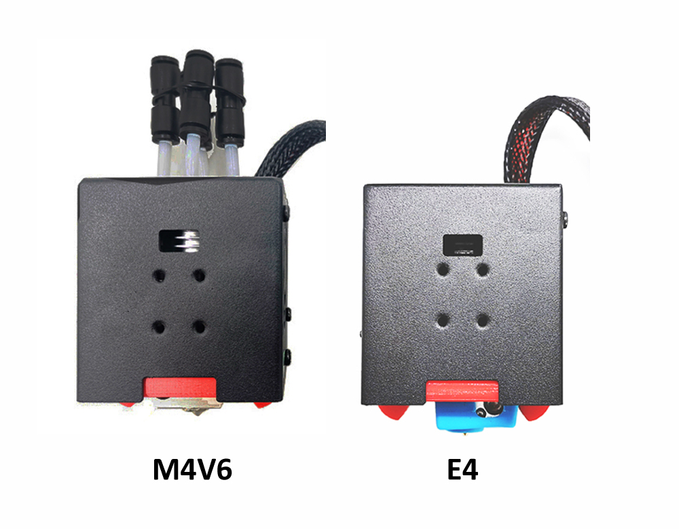
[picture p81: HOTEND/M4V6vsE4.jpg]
   
- **M4 핫엔드**는 다양한 색상의 필라멘트를 혼합하여 새로운 색상의 필라멘트를 생성할 수 있습니다. **E4 hotend**에는 이 기능이 없습니다.
- **E4 hotend**는 단색 또는 다중 색상 3D 개체(최대 4색)를 인쇄하는 데 적합합니다.
- **M4 핫엔드**는 그라데이션 색상의 3D 개체를 인쇄하는 데 적합하며 4콜로 이상의 3D 개체도 인쇄할 수 있습니다(필라멘트를 혼합하여).
### E4 핫엔드의 작동 원리

### M4 핫엔드의 작동 원리
[](https://github.com/ZONESTAR3D/Document-and-User-Guide/assets/29502731/2b9f4d75-b6fd-486f-aaa7-7a1163383316)

### E4 핫엔드의 장점
1. 다중 색상 3D 개체를 인쇄하는 동안 더 작은 "압출기 스위치 프라임 타워".
2. 단일 색상의 3D 개체를 인쇄할 때 품질이 향상됩니다.
3. 동일한 3D 물체에 다양한 유형의 필라멘트를 인쇄할 수 있습니다.
### M4 핫엔드의 장점
1. 다양한 색상의 필라멘트를 새로운 색상으로 혼합하는 기능을 지원합니다.
2. 그라데이션 컬러 인쇄를 지원합니다.
3. 더 높은 유량을 지원합니다.
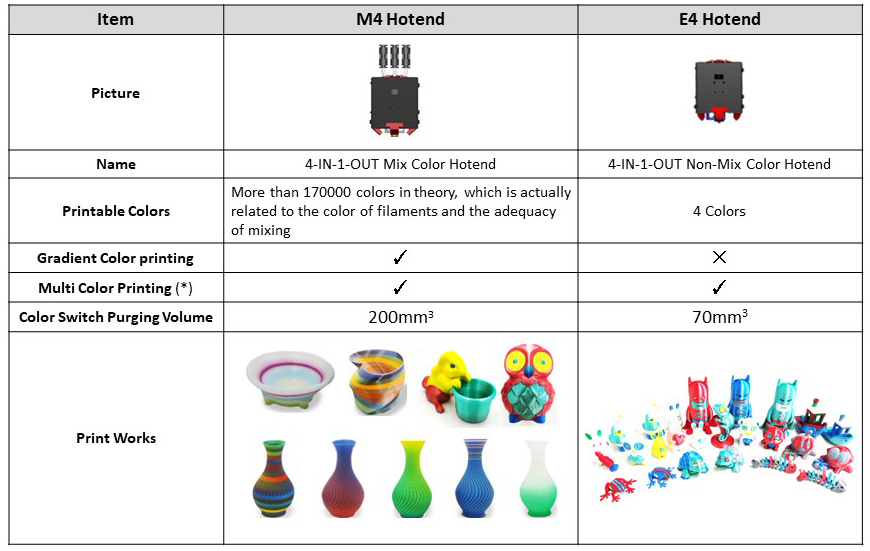
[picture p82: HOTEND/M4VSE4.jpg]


-----
## <a id="a2"> M4와 E4 중 어떤 핫엔드를 선택해야 하나요?</a>
- 그라디언트 색상 3D 모델을 인쇄할 **필요가 없는** 경우 **E4 핫엔드**를 선택하는 것이 좋습니다. 단일 색상 및 다중 색상 3D 인쇄를 인쇄할 때 더 나은 품질을 얻을 수 있습니다.
- **그라디언트 색상** 3D 모델을 인쇄하고 싶거나 **다른 색상의 필라멘트를 다른 색상으로 혼합**하려면 M4 핫엔드를 선택하세요.

-----
## <a id="a3"> 필라멘트를 올바르게 로드/언로드하는 방법</a>
M4 핫엔드와 E4 핫엔드는 필라멘트 로딩에 대한 요구 사항이 다릅니다.
- **필라멘트 로딩 수량 요구사항:**
   - M4 핫엔드는 단색 또는 다중 색상 인쇄 여부에 관계없이 동시에 4개의 필라멘트를 로드해야 합니다.
   - E4 핫엔드는 인쇄된 색상에 따라 로드할 필라멘트 수를 선택할 수 있습니다.
- **필라멘트 로딩 위치 요구 사항:**
   - M4 핫엔드는 핫엔드 하단에 필라멘트를 설치해야 합니다.
   - E4 핫 엔드는 핫 엔드의 깔때기 입구 위에 필라멘트를 설치해야 합니다(PTFE 튜브를 약 20mm 연장).
### M4 핫엔드용
#### M4 핫엔드에 필라멘트를 로드하는 단계:
##### (https://www.youtube.com/watch?v=-47yB95uIxI)
M4 핫엔드에 필라멘트를 로드할 때 프린팅 중에 사용해야 하는 압출기 수에 관계없이 ***필라멘트 4개를 모두 핫엔드에 로드해야 하며*** 모든 필라멘트가 제대로 작동하는지 확인하는 것이 중요합니다. 인쇄를 시작하기 전에 핫엔드*** 하단에 로드합니다.     
:warning: ***단색 또는 다중 색상으로 인쇄하든 상관없이 4개의 필라멘트를 모두 M4V6 핫엔드에 로드해야 합니다.***
1. 필라멘트를 압출기와 핫엔드에 장착하기 전에 대각선 펜치로 필라멘트의 앞부분을 자릅니다.
2. 모든 Extruder에 4개의 필라멘트를 하나씩 장착한 후 필라멘트가 핫엔드의 내부 PTFE 튜브에 들어갈 때까지 Extruder의 기어를 회전시킨 후 4~5바퀴 더 회전한 후 정지합니다.

#### M4 핫엔드에서 필라멘트를 언로드하는 단계:
1. 노즐을 가열(PLA는 200℃ / PETG/ABS는 230℃)하고 온도가 도달할 때까지 기다립니다. ***Menu: Prepare>>Filament>>Preheat: 200/230***
2. 4개 채널 모두에 동시에 최소 10mm의 필라멘트를 공급합니다. ***Menu: Prepare>>Filament>>Extruder: All; Prepare>>Filament>>Slowly Load***
3. 핫엔드에서 필라멘트를 언로드합니다. ***Menu: Prepare>>Filament>>Slowly unload***
  
### E4 핫엔드의 경우
#### <a id = "PRELOAD_FILAMENT">E4 핫엔드에 필라멘트를 로드하는 단계:</a>
##### (https://www.youtube.com/watch?v=FyHrAMytlT8)
E4 핫엔드의 작동 원리를 이해했다면 다중 색상을 인쇄할 때 기계가 먼저 핫엔드에서 이전에 로드한 필라멘트를 언로드한 후 다음 필라멘트를 로드해야 한다는 것을 이미 알고 있어야 합니다. 그러나 일반적으로 ***프린팅을 시작하기 전에 필라멘트 앞부분과 노즐 사이의 거리를 인식하는 기능이 기계에 없습니다***. 따라서 <u>***"필라멘트 사전 로드"***</u>라는 프로세스를 설정해야 합니다. 이는 기계가 이전에 기계에 알려진 적절한 위치로 미세한 실을 이동할 수 있도록 하는 것을 목표로 합니다. 개체를 인쇄합니다.
:warning: ***gcode 파일에 사용해야 하는 압출기의 필라멘트만 E4 핫엔드에 로드해야 합니다.***

### E4 핫엔드에서 필라멘트를 언로드하는 단계:
1. 노즐을 가열(PLA는 200℃ / PETG/ABS는 230℃)하고 온도가 도달할 때까지 기다립니다. ***Menu: Prepare>>Filament>>Preheat: 200/230***
2. 사용한 Extruder에 필라멘트를 10mm 이상 공급합니다. ***Menu: Prepare>>Filament>>Extruder: 1/2/3/4; Prepare>>Filament>>Slowly Load***
3. 핫엔드에서 필라멘트를 꺼냅니다. ***Menu: Prepare>>Filament>>Slowly unload***

-----
## <a id = "a4">M4와 E4 핫엔드의 슬라이싱 설정 차이점은 무엇입니까:</a>
:pushpin: 이 설정은 당사가 제공하는 PrusaSlicer 소프트웨어의 프로필에 설정되어 있습니다. 귀하의 기계와 핫엔드 유형에 따라 올바른 **프린터 사전 설정**을 선택하기만 하면 됩니다.
### 다색 인쇄를 위한 슬라이스 설정
다중 색상 인쇄의 경우 E4 핫엔드와 M4 핫엔드의 슬라이싱 설정은 주로 다음과 같이 다릅니다.
- **gcode 시작**
   - **E4 핫엔드**의 경우 프린팅을 시작하기 전에 "필라멘트를 미리 로드"해야 합니다([**이유를 알다**](#PRELOAD_FILAMENT)). 자세한 내용은 [**E4의 시작 gcode를 참조하세요. 핫엔드**][E4_STARTGCODE].
   - **M4 핫엔드**의 경우 4색 이하로 인쇄하는 경우 시작 gcode를 특별히 변경할 필요가 없습니다. 하지만 **4개 이상의 색상을 인쇄해야 하는 경우**(다른 색상의 필라멘트를 여러 색상으로 혼합) 시작 gcode에서 색상 혼합 비율을 설정할 수 있습니다. 자세한 내용은 [**M4 핫엔드를 사용하여 4색 이상 인쇄하는 방법**][M4_MIXMULTICOLORPRINT]을 참조하세요.
- **압출기의 후퇴 설정**
   - **E4 핫엔드**의 경우 권장 **후퇴 길이**는 6~8mm(10mm 미만이어야 함)입니다.
   - **M4 핫엔드**의 권장 **후퇴 길이**는 8~15mm입니다.
- **와이프 타워(프라임 타워)**      
:pushpin: 여러 압출기 프린터를 지원하는 슬라이싱 소프트웨어에는 **"Wipe Tower(프라임 타워)"** 옵션이 있습니다. 프린터가 한 압출기에서 다른 압출기로 전환할 때 먼저 핫 엔드에 있는 이전 색상의 가는 실을 청소해야 하는 경우가 많기 때문입니다. 삭제 타워 옵션을 켠 후 슬라이싱 소프트웨어는 gcode 파일에 "추가" 인쇄물을 생성하여 핫 엔드에 남아 있는 필라멘트를 정리할 수 있습니다.
   - **E4 핫엔드**의 경우 와이어 타워에 필요한 부피가 상대적으로 작습니다.
   - **M4 핫엔드**의 경우 와이어 타워에 필요한 부피가 상대적으로 큽니다.
- **공구 변경 G 코드**
   - **E4 핫엔드**의 경우 Extruder를 전환할 때 이전 컬러 필라멘트를 핫엔드에서 빼낸 후 다음 컬러 필라멘트를 핫엔드에 장착해야 합니다. 따라서 이 작업을 수행하려면 도구 변경 Gcode를 설정해야 합니다. 자세한 내용은 [**E4 핫엔드용 공구 변경 G 코드**][E4_TOOLCHANGE]를 참조하세요.
   - **M4 핫엔드**의 경우 **공구 변경 G 코드**가 필요하지 않습니다.

-----
## <a id="a5"> M4 핫엔드와 E4 핫엔드 간 전환 방법</a>
### 1. 핫엔드 하우징에 있는 나사 3개를 풀고 기계(x 풀리)에서 기존 핫엔드를 제거합니다. 그런 다음 새 핫엔드를 기계(x 풀리)에 설치하고 나사를 잠급니다.
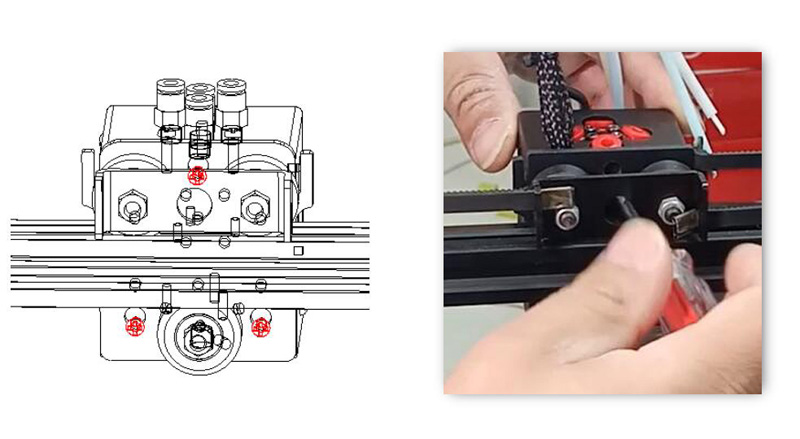
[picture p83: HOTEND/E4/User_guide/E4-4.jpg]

### 2. 새로운 핫엔드의 전선을 기계에 연결합니다.
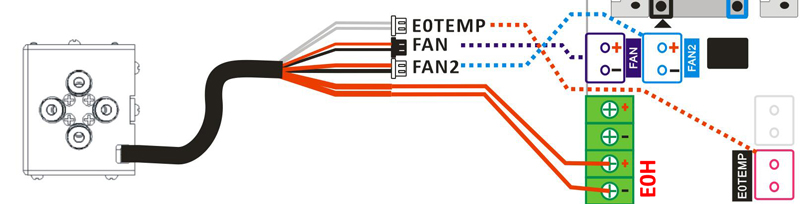
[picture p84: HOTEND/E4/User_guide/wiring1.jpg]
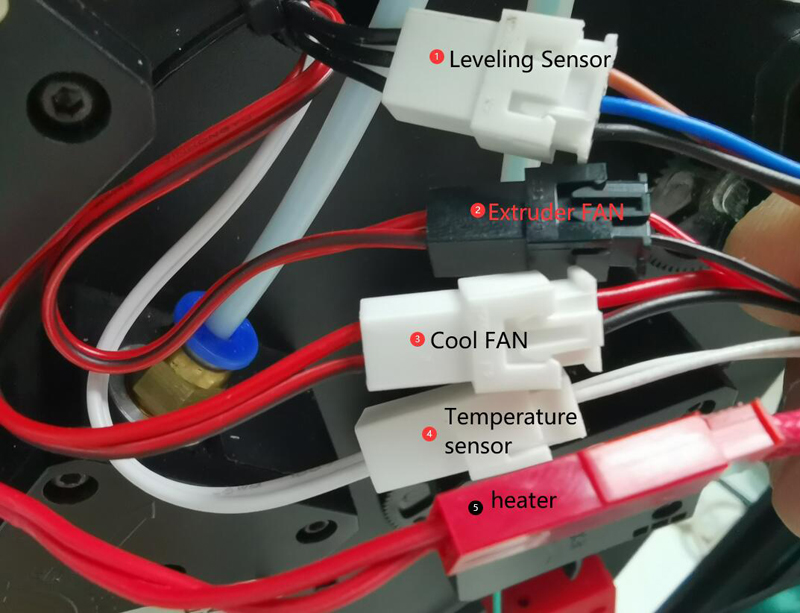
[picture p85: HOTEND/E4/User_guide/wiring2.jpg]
 
### 3. LCD 메뉴에서 핫엔드 유형을 설정합니다: *control>>Configure>>Hotend Type*
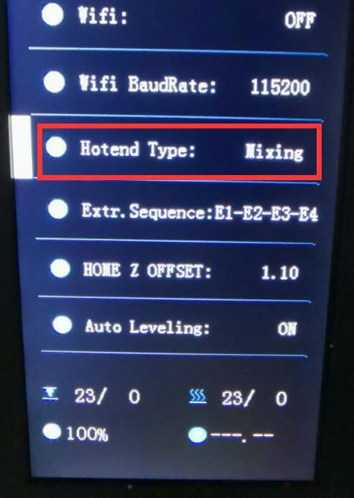
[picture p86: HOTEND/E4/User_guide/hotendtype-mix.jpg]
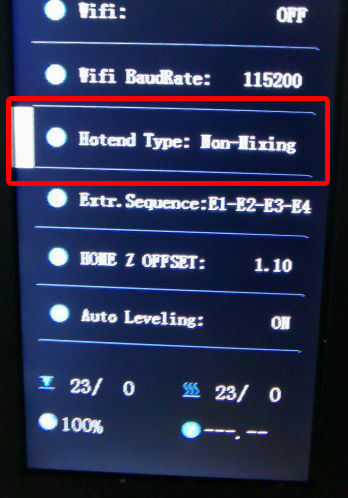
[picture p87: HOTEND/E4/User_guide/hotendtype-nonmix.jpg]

#### :pushpin: Z9V5 프린트 헤드의 커넥터는 기계 내부에 숨겨져 있으므로 고무 링을 제거하고 커넥터를 당겨야 합니다.
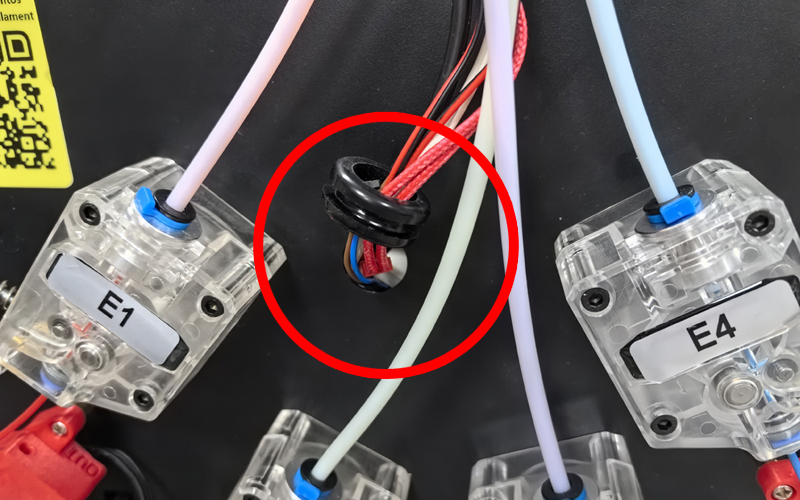
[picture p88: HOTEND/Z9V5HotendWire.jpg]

### :warning: 참고 1: LCD 화면에서 "핫엔드 유형" 메뉴를 찾을 수 없는 경우 최신 펌웨어를 프린터에 업로드하십시오.
[**:point_right: Z9V5용 펌웨어**][FW_Z9V5] / [**:point_right: Z8P용 펌웨어**][FW_Z8P] / [**:point_right: Z9M4용 펌웨어**][FW_Z9M4]
### :warning: 참고 2: 혼합 색상 핫엔드와 비혼합 색상 핫엔드는 서로 다른 슬라이스 설정을 사용해야 하므로 구별에 주의하십시오. 잘못된 슬라이스 설정을 사용하면 핫엔드가 차단될 수 있습니다.

-----

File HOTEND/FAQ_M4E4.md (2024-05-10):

[E4_STARTGCODE]: https://github.com/ZONESTAR3D/Slicing-Guide/blob/master/PrusaSlicer/Custom_Gcode.md#start-g-code
[M4_MIXMULTICOLORPRINT]: https://github.com/ZONESTAR3D/Slicing-Guide/blob/master/PrusaSlicer/PrusaSlicerGuide_M4.md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
[E4_TOOLCHANGE]: https://github.com/ZONESTAR3D/Slicing-Guide/blob/master/PrusaSlicer/Custom_Gcode.md#tool-change-g-code
[FW_Z9V5]: https://github.com/ZONESTAR3D/Firmware/tree/master/Z9/Z9V5/bin
[FW_Z9M4]: https://github.com/ZONESTAR3D/Firmware/tree/master/Z9/Z9M4
[FW_Z8P]: https://github.com/ZONESTAR3D/Firmware/tree/master/Z8/Z8P

----
## <a id="choose-language">:globe_with_meridians: Choose language </a>









<!-- [![](../lanpic/SA.png)](https://github.com/ZONESTAR3D/Upgrade-kit-guide/tree/main/HOTEND/FAQ_M4E4-ar.md) -->

----
# FAQ for E4 and M4 hotend
- [**What's the different between E4 and M4 hotend?**](#a1)
- [**Which type of hotend should I choose?**](#a2)
- [**How to load filaments into the hotend correctly?**](#a3)
- [**What is the difference in slicing settings between M4 and E4 hotends**](#a4)
- [**How to switch between M4 and E4 hotend?**](#a5)

-----
## <a id="a1">What's different between E4 and M4 hotend?</a>
   
- **M4 hotend** can mix different colored filaments to produce new colored filaments. **E4 hotend** does not have this ability.  
- **E4 hotend** is good at printing one color or multi color 3d object (up to 4 color).
- **M4 hotend** is good at printing gradient color 3d object, it can print more than 4 colos 3d object too (by mixing the filaments).
### Working principle of E4 hotend

### Working principle of M4 hotend
[](https://github.com/ZONESTAR3D/Document-and-User-Guide/assets/29502731/2b9f4d75-b6fd-486f-aaa7-7a1163383316)

### Advantages of E4 hotend
1. Smaller "extruder switch prime tower" while printing multi color 3d object.
2. Better quality when printing one color 3d object.
3. Support to print different type of filament on the same 3d object.
### Advantages of M4 hotend
1. Support mixing different color filaments to new colors.
2. Support gradient color printing.
3. Support higher flow rate.


-----
## <a id="a2"> Which hotend should I choose, M4 or E4?</a>
- If you **do not need** to print gradient color 3d model, we suggest you choose **E4 hotend**, it can get better quality on printing single color and multi colors 3d prints.
- If you want to print **gradient color** 3d model, or you want to **mix different color filaments to another color**, choose M4 hotend.

-----
## <a id="a3"> How to load/unload filaments correctly</a>
M4 hot end and E4 hot end have different requirements for loading filament. 
- **Requirements of quantity for loading filaments:**
  - The M4 hot end requires four filaments to be loaded at the same time, regardless of whether printing single color or multi-color; 
  - The E4 hot end can choose the number of filaments to load according to the colors printed.   
- **Requirements of position for loading filaments:**
  - The M4 hot end requires the filament to be installed at the bottom of the hot end; 
  - The E4 hot end requires the filament to be installed above the funnel mouth of the hot end (extending the PTFE tube by about 20mm).
### For M4 Hotend
#### Steps to load filaments into the M4 hotend:
##### (https://www.youtube.com/watch?v=-47yB95uIxI)
When loading the filaments into the M4 hotend, regardless of how many extruders you need to use during printing, ***all four filaments must be loaded into the hotend***, and it is important to  ***ensure that all filaments are loaded into the bottom of the hotend*** before starting printing.     
:warning: ***Whether printing in single color or multi-color, you need to load all four filaments into the M4V6 hotend.***     
1. Cut the front of the filament with diagonal pliers before loading it to the extruder and hotend.
2. Load 4 filaments to all extruders one by one and then rotate the gear of the extruders until the filament enter to the inner PTFE tube of hotend, rotate more 4 ~ 5 turn and then stop.     

#### Steps to unload filament from the M4 hotend:
1. Heating the nozzle (200℃ for PLA / 230℃ for PETG/ABS) and wait for the temperature to reach. ***Menu: Prepare>>Filament>>Preheat: 200/230***
2. Feed filaments at least 10mm on all 4 channels simultaneously. ***Menu: Prepare>>Filament>>Extruder: All; Prepare>>Filament>>Slowly Load***
3. Unload filaments from the hotend. ***Menu: Prepare>>Filament>>Slowly unload***    

### For E4 Hotend
#### <a id = "PRELOAD_FILAMENT">Steps to load filaments into the E4 hotend:</a>
##### (https://www.youtube.com/watch?v=FyHrAMytlT8)
If you understand the working principle of the E4 hotend, you should already know that when printing multi-color, the machine first needs to unload the previously loaded filament from the hotend and then load the next filament. However, usually ***the machine does not have the ability to recognize the distance between the front end of the filament and the nozzle before starting printing***. Therefore, we need to set up a process called <u>***"pre-load filaments"***</u>, which aims to allow the machine to move the fine threads to a suitable position known to the machine before printing the object.      
:warning: ***Only the filaments on the extruder that need to be used in the gcode file need to be loaded into the E4 hotend.***      

### Steps to unload filament from the E4 hotend:
1. Heating the nozzle (200℃ for PLA / 230℃ for PETG/ABS). ***Menu: Prepare>>Filament>>Preheat: 200/230***
2. Feed filament at least 10mm on the used extruder. ***Menu: Prepare>>Filament>>Extruder: 1/2/3/4; Prepare>>Filament>>Slowly Load***
3. Unload filament from the hotend. ***Menu: Prepare>>Filament>>Slowly unload***

-----
## <a id = "a4">What is the difference in slicing settings between M4 and E4 hotend:</a>
:pushpin: These settings have been set in the profiles of the PrusaSlicer software we provide. You only need to choose the correct **printer preset** according to your machine and hotend type.
### Slice settings for multi-color printing    
For printing multi-color, the slicing settings for the E4 hotend and M4 hotend mainly differ as follows:
- **start gcode**
  - **For the E4 hotend**, it requires "pre-load filaments" before starting printing([**Know Why**](#PRELOAD_FILAMENT)), for details, please refer to [**start gcode of the E4 hotend**][E4_STARTGCODE].     
  - **For the M4 hotend**, When printing no more than 4 colors, there is no need to make special changes to the start gcode. But **if you need to print more than 4 colors** (mixing different colored filaments into multiple colors), you can set the color mixing ratio in the start gcode. For details, please refer to [**How to print more than 4 colors by using M4 hot end**][M4_MIXMULTICOLORPRINT].
- **Retraction settings of the Extruders**
  - **For the E4 hotend**, the recommended **Retraction length** is 6 ~ 8mm (must be less than 10mm).
  - **For the M4 hotend**, the recommended **Retraction length** is 8 ~ 15mm.
- **Wipe Tower (Prime Tower)**     
:pushpin: The slicing software that supports multiple extruder printers has an **"Wipe Tower(Prime Tower)"** option. Because when the printer switches from one extruder to another, it often needs to first clean the fine threads of the previous color in the hot end. After turning on the erase tower option, the slicing software can generate an "additional" print in the gcode file to clean up any remaining filaments in the hot end.
  - **For the E4 hotend**, the required volume of the wire tower is relatively small.
  - **For the M4 hotend**, the required volume of the wire tower is relatively big.
- **Tool change G-code**
  - **For the E4 hotend**, when switching the extruder, it is necessary to pull out the previous color filament from the hotend and then load the next color filament to the hotend. Therefore, Tool Change Gcode needs to be set to achieve this operation. For deltails, please refer to [**Tool change G-code for E4 hotend**][E4_TOOLCHANGE].
  - **For the M4 hotend**, it doesn't need **Tool change G-code**.

-----
## <a id="a5"> How to switch between M4 hotend and E4 hotend</a>
### 1. Loosen the three screws on the hotend housing and remove the old hotend from the machine (x pulley). Then install the new hotend on the machine (x pulley) and lock the screws.

### 2. Connect the wires of the new hotend to the machine.
 
### 3. Set the hotend type on the LCD menu: *Control>>Configure>>Hotend Type*

#### :pushpin: The connectors of the Z9V5 print head are hidden inside the machine, you need to remove the rubber ring and pull out the connectors.

### :warning: NOTE 1: If you can't find the "hotend type" menu on LCD screen, please upload the newest firmware to your printer. 
[**:point_right: Firmware for Z9V5**][FW_Z9V5] / [**:point_right: Firmware for Z8P**][FW_Z8P] / [**:point_right: Firmware for Z9M4**][FW_Z9M4] 
### :warning: NOTE 2: The mix color Hotend and non-mix color hotend must use different slice settings, please pay attention to distinguish. Using the wrong slice setting may block the hotend.

-----

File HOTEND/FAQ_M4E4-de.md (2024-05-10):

[E4_STARTGCODE]: https://github.com/ZONESTAR3D/Slicing-Guide/blob/master/PrusaSlicer/Custom_Gcode.md#start-g-code
[M4_MIXMULTICOLORPRINT]: https://github.com/ZONESTAR3D/Slicing-Guide/blob/master/PrusaSlicer/PrusaSlicerGuide_M4.md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
[E4_TOOLCHANGE]: https://github.com/ZONESTAR3D/Slicing-Guide/blob/master/PrusaSlicer/Custom_Gcode.md#tool-change-g-code
[FW_Z9V5]: https://github.com/ZONESTAR3D/Firmware/tree/master/Z9/Z9V5/bin
[FW_Z9M4]: https://github.com/ZONESTAR3D/Firmware/tree/master/Z9/Z9M4
[FW_Z8P]: https://github.com/ZONESTAR3D/Firmware/tree/master/Z8/Z8P

----
## <a id="choose-language">:globe_with_meridians: Choose language </a>









<!-- [![](../lanpic/SA.png)](https://github.com/ZONESTAR3D/Upgrade-kit-guide/tree/main/HOTEND/FAQ_M4E4-ar.md) -->

----
# FAQ für E4- und M4-Hotend
- [**Was ist der Unterschied zwischen E4- und M4-Hotend?**](#A1)
- [**Welche Art von Hotend soll ich wählen?**](#A2)
- [**Wie lade ich Filamente richtig in das Hotend?**](#A3)
- [**Was ist der Unterschied in den Slicing-Einstellungen zwischen M4- und E4-Hotends**](#A4)
- [**Wie wechselt man zwischen M4- und E4-Hotend?**](#A5)

-----
## <a id="A1">Was ist der Unterschied zwischen E4- und M4-Hotend?</a>
   
- **M4 Hotend** kann verschiedenfarbige Filamente mischen, um neue farbige Filamente herzustellen. **E4 Hotend** verfügt nicht über diese Fähigkeit.
- **E4 Hotend** eignet sich gut zum Drucken von ein- oder mehrfarbigen 3D-Objekten (bis zu 4 Farben).
- **M4 Hotend** eignet sich gut zum Drucken von 3D-Objekten mit Farbverlauf, es kann auch 3D-Objekte mit mehr als 4 Farben drucken (durch Mischen der Filamente).
### Funktionsprinzip des E4-Hotends

### Funktionsprinzip des M4-Hotends
[](https://github.com/ZONESTAR3D/Document-and-User-Guide/assets/29502731/2b9f4d75-b6fd-486f-aaa7-7a1163383316)

### Vorteile des E4-Hotends
1. Kleinerer „Extruder Switch Prime Tower“ beim Drucken mehrfarbiger 3D-Objekte.
2. Bessere Qualität beim Drucken von einfarbigen 3D-Objekten.
3. Unterstützung für das Drucken verschiedener Filamenttypen auf demselben 3D-Objekt.
### Vorteile des M4-Hotends
1. Unterstützen Sie das Mischen verschiedener Farbfilamente zu neuen Farben.
2. Unterstützt Farbverlaufsdruck.
3. Unterstützen Sie eine höhere Durchflussrate.


-----
## <a id="A2">Welches Hotend soll ich wählen, M4 oder E4?</a>
- Wenn Sie kein 3D-Modell mit Farbverlauf drucken müssen, empfehlen wir Ihnen, das **E4-Hotend** zu wählen, da es beim Drucken von einfarbigen und mehrfarbigen 3D-Drucken eine bessere Qualität erzielen kann.
- Wenn Sie ein 3D-Modell mit **Farbverlauf** drucken oder **unterschiedliche Farbfilamente zu einer anderen Farbe mischen möchten**, wählen Sie das M4-Hotend.

-----
## <a id="A3">So laden/entladen Sie Filamente richtig</a>
M4-Hot-End und E4-Hot-End haben unterschiedliche Anforderungen an das Laden des Filaments.
- **Anforderungen an die Menge zum Laden von Filamenten:**
   - Das M4-Hot-End erfordert das gleichzeitige Laden von vier Filamenten, unabhängig davon, ob einfarbig oder mehrfarbig gedruckt wird.
   - Das E4-Hot-End kann die Anzahl der zu ladenden Filamente entsprechend den gedruckten Farben wählen.
- **Anforderungen an die Position zum Laden von Filamenten:**
   - Für das M4-Hot-End muss das Filament an der Unterseite des Hot-Ends installiert werden.
   - Für das E4-Hot-End muss das Filament über der Trichtermündung des Hot-Ends installiert werden (wodurch der PTFE-Schlauch um etwa 20 mm verlängert wird).
### Für M4 Hotend
#### Schritte zum Laden von Filamenten in das M4-Hotend:
##### (https://www.youtube.com/watch?v=-47yB95uIxI)
Beim Laden der Filamente in das M4-Hotend müssen, unabhängig davon, wie viele Extruder Sie beim Drucken verwenden müssen, ***alle vier Filamente in das Hotend geladen werden***, und es ist wichtig, ***sicherzustellen, dass alle Filamente vorhanden sind in die Unterseite des Hotends*** eingelegt werden, bevor mit dem Drucken begonnen wird.    
:warning: ***Egal, ob Sie einfarbig oder mehrfarbig drucken, Sie müssen alle vier Filamente in das M4V6-Hotend laden.***
1. Schneiden Sie die Vorderseite des Filaments mit einer Diagonalzange ab, bevor Sie es in den Extruder und das Hotend laden.
2. Laden Sie nacheinander 4 Filamente in alle Extruder und drehen Sie dann das Zahnrad des Extruders, bis das Filament in das innere PTFE-Rohr des Hotends gelangt. Drehen Sie weitere 4 bis 5 Umdrehungen und stoppen Sie dann.

#### Schritte zum Entladen des Filaments aus dem M4-Hotend:
1. Erhitzen Sie die Düse (200℃ für PLA / 230℃ für PETG/ABS) und warten Sie, bis die Temperatur erreicht ist. ***Menu: Prepare>>Filament>>Preheat: 200/230***.
2. Führen Sie Filamente mindestens 10 mm gleichzeitig auf allen 4 Kanälen zu. ***Menu: Prepare>>Filament>>Extruder: All; Prepare>>Filament>>Slowly Load***;
3. Filamente aus dem Hotend entladen ***Menu: Prepare>>Filament>>Slowly unload***.
  
### Für E4 Hotend
#### <a id = "PRELOAD_FILAMENT">Schritte zum Laden von Filamenten in das E4-Hotend:</a>
##### (https://www.youtube.com/watch?v=FyHrAMytlT8)
Wenn Sie das Funktionsprinzip des E4-Hotends verstehen, sollten Sie bereits wissen, dass das Gerät beim Mehrfarbendruck zunächst das zuvor geladene Filament aus dem Hotend entladen und dann das nächste Filament laden muss. Normalerweise ist das Gerät jedoch nicht in der Lage, den Abstand zwischen dem vorderen Ende des Filaments und der Düse zu erkennen, bevor es mit dem Drucken beginnt.*** Daher müssen wir einen Prozess namens <u>***„Filamente vorladen“***</u> einrichten, der es der Maschine ermöglichen soll, die feinen Fäden an eine geeignete Position zu bewegen, die der Maschine zuvor bekannt ist Drucken des Objekts.
:warning: ***Nur die Filamente am Extruder, die in der Gcode-Datei verwendet werden müssen, müssen in das E4-Hotend geladen werden.***

### Schritte zum Entladen des Filaments aus dem E4-Hotend:
1. Erhitzen Sie die Düse (200℃ für PLA / 230℃ für PETG/ABS) und warten Sie, bis die Temperatur erreicht ist. ***Menu: Prepare>>Filament>>Preheat: 200/230***
2. Führen Sie dem verwendeten Extruder mindestens 10 mm Filament zu. ***Menu: Prepare>>Filament>>Extruder: 1/2/3/4; Prepare>>Filament>>Slowly Load***   
3. Entladen Sie das Filament vom Hotend. ***Menu: Prepare>>Filament>>Slowly unload***    

-----
## <a id = "A4">Was ist der Unterschied in den Slicing-Einstellungen zwischen M4- und E4-Hotend:</a>
:pushpin: Diese Einstellungen wurden in den Profilen der von uns bereitgestellten PrusaSlicer-Software festgelegt. Sie müssen nur die richtige **Druckervoreinstellung** entsprechend Ihrem Gerät und Hotend-Typ auswählen.
### Slice-Einstellungen für Mehrfarbendruck
Für den Mehrfarbendruck unterscheiden sich die Slicing-Einstellungen für das E4-Hotend und das M4-Hotend hauptsächlich wie folgt:
- **Gcode starten**
   - **Für das E4-Hotend** ist vor dem Drucken ein Vorladen der Filamente erforderlich ([**Know Why**](#PRELOAD_FILAMENT)), Einzelheiten finden Sie im [**Start-Gcode des E4 hotend**][E4_STARTGCODE].
   - **Für das M4-Hotend**: Wenn nicht mehr als 4 Farben gedruckt werden, müssen keine besonderen Änderungen am Start-Gcode vorgenommen werden. Aber **wenn Sie mehr als 4 Farben drucken müssen** (also verschiedenfarbige Filamente zu mehreren Farben mischen), können Sie das Farbmischungsverhältnis im Start-Gcode festlegen. Einzelheiten finden Sie unter [**So drucken Sie mehr als 4 Farben mit dem M4-Hot-End**][M4_MIXMULTICOLORPRINT].
- **Retraktionseinstellungen der Extruder**
   - **Für das E4-Hotend** beträgt die empfohlene **Rückzugslänge** 6 ~ 8 mm (muss weniger als 10 mm betragen).
   - **Für das M4-Hotend** beträgt die empfohlene **Rückzugslänge** 8 ~ 15 mm.
- **Wipe Tower (Prime Tower)**
:pushpin: Die Slicing-Software, die mehrere Extruderdrucker unterstützt, verfügt über die Option **Wipe Tower (Prime Tower)**. Denn wenn der Drucker von einem Extruder zum anderen wechselt, muss er oft zunächst die feinen Fäden der vorherigen Farbe im Hotend reinigen. Nach dem Einschalten der Löschturm-Option kann die Slicing-Software einen zusätzlichen Druck in der Gcode-Datei erzeugen, um alle verbleibenden Filamente im heißen Ende zu entfernen.
   - **Für das E4-Hotend** ist das erforderliche Volumen des Drahtturms relativ gering.
   - **Für das M4-Hotend** ist das benötigte Volumen des Drahtturms relativ groß.
- **Werkzeugwechsel-G-Code**
   - **Beim E4-Hotend** ist es beim Wechseln des Extruders erforderlich, das vorherige Farbfilament aus dem Hotend herauszuziehen und dann das nächste Farbfilament in das Hotend zu laden. Daher muss der Werkzeugwechsel-Gcode festgelegt werden, um diesen Vorgang auszuführen. Einzelheiten finden Sie unter [**Werkzeugwechsel-G-Code für E4-Hotend**][E4_TOOLCHANGE].
   - **Für das M4-Hotend** ist kein **Werkzeugwechsel-G-Code** erforderlich.

-----
## <a id="A5">So wechseln Sie zwischen M4-Hotend und E4-Hotend</a>
### 1. Lösen Sie die drei Schrauben am Hotend-Gehäuse und entfernen Sie das alte Hotend von der Maschine (x Riemenscheibe). Installieren Sie dann das neue Hotend an der Maschine (X-Riemenscheibe) und ziehen Sie die Schrauben fest.

### 2. Schließen Sie die Kabel des neuen Hotends an die Maschine an.
 
### 3. Stellen Sie den Hotend-Typ im LCD-Menü ein: *Steuerung>>Konfigurieren>>Hotend-Typ*

#### :pushpin: Die Anschlüsse des Z9V5-Druckkopfs sind im Inneren des Geräts versteckt. Sie müssen den Gummiring entfernen und die Anschlüsse herausziehen.

### :warning: HINWEIS 1: Wenn Sie das Menü „Hotend-Typ“ nicht auf dem LCD-Bildschirm finden können, laden Sie bitte die neueste Firmware auf Ihren Drucker hoch.
[**:point_right: Firmware für Z9V5**][FW_Z9V5] / [**:point_right: Firmware für Z8P**][FW_Z8P] / [**:point_right: Firmware für Z9M4**][FW_Z9M4]
### :warning: HINWEIS 2: Das Mischfarben-Hotend und das Nicht-Mischfarben-Hotend müssen unterschiedliche Slice-Einstellungen verwenden. Bitte achten Sie auf die Unterscheidung. Die Verwendung der falschen Slice-Einstellung kann das Hotend blockieren.

-----

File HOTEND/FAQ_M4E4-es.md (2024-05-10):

[E4_STARTGCODE]: https://github.com/ZONESTAR3D/Slicing-Guide/blob/master/PrusaSlicer/Custom_Gcode.md#start-g-code
[M4_MIXMULTICOLORPRINT]: https://github.com/ZONESTAR3D/Slicing-Guide/blob/master/PrusaSlicer/PrusaSlicerGuide_M4.md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
[E4_TOOLCHANGE]: https://github.com/ZONESTAR3D/Slicing-Guide/blob/master/PrusaSlicer/Custom_Gcode.md#tool-change-g-code
[FW_Z9V5]: https://github.com/ZONESTAR3D/Firmware/tree/master/Z9/Z9V5/bin
[FW_Z9M4]: https://github.com/ZONESTAR3D/Firmware/tree/master/Z9/Z9M4
[FW_Z8P]: https://github.com/ZONESTAR3D/Firmware/tree/master/Z8/Z8P

----
## <a id="choose-language">:globe_with_meridians: Choose language </a>









<!-- [![](../lanpic/SA.png)](https://github.com/ZONESTAR3D/Upgrade-kit-guide/tree/main/HOTEND/FAQ_M4E4-ar.md) -->

----
# Preguntas frecuentes sobre hotend E4 y M4
- [**¿Cuál es la diferencia entre el hotend E4 y M4?**](#A1)
- [**¿Qué tipo de hotend debo elegir?**](#A2)
- [**¿Cómo cargar filamentos en el hotend correctamente?**](#A3)
- [**¿Cuál es la diferencia en la configuración de corte entre los hotends M4 y E4**](#A4)
- [**¿Cómo cambiar entre el hotend M4 y E4?**](#A5)

-----
## <a id="A1">¿Qué diferencia hay entre el hotend E4 y M4?</a>
   
- **M4 hotend** puede mezclar filamentos de diferentes colores para producir filamentos de nuevos colores. **El hotend E4** no tiene esta capacidad.
- **E4 hotend** es bueno para imprimir objetos 3D de un color o de varios colores (hasta 4 colores).
- **M4 hotend** es bueno para imprimir objetos 3D de color degradado, también puede imprimir objetos 3D de más de 4 colores (mezclando los filamentos).
### Principio de funcionamiento del hotend E4

### Principio de funcionamiento del hotend M4
[](https://github.com/ZONESTAR3D/Document-and-User-Guide/assets/29502731/2b9f4d75-b6fd-486f-aaa7-7a1163383316)

### Ventajas del hotend E4
1. "Torre principal del interruptor del extrusor" más pequeña mientras se imprimen objetos 3D multicolores.
2. Mejor calidad al imprimir objetos 3D de un color.
3. Soporte para imprimir diferentes tipos de filamento en el mismo objeto 3D.
### Ventajas del hotend M4
1. Admite mezclar filamentos de diferentes colores con nuevos colores.
2. Admite impresión en color degradado.
3. Admite un mayor caudal.


-----
## <a id="A2"> ¿Qué hotend debo elegir, M4 o E4?</a>
- Si **no necesita** imprimir un modelo 3D de color degradado, le sugerimos que elija **E4 hotend**, puede obtener una mejor calidad en la impresión de impresiones 3D de un solo color y de varios colores.
- Si desea imprimir un modelo 3D de **color degradado**, o desea **mezclar filamentos de diferentes colores con otro color**, elija el hotend M4.

-----
## <a id="A3">Cómo cargar/descargar filamentos correctamente</a>
El extremo caliente M4 y el extremo caliente E4 tienen diferentes requisitos para cargar filamento.
- **Requisitos de cantidad para carga de filamentos:**
   - El hot end M4 requiere cargar cuatro filamentos al mismo tiempo, independientemente de si imprime en un solo color o en varios colores;
   - El hot end E4 puede elegir el número de filamentos a cargar según los colores impresos.
- **Requisitos de posición para carga de filamentos:**
   - El hot end M4 requiere que el filamento se instale en la parte inferior del hot end;
   - El hot end E4 requiere que el filamento se instale encima de la boca del embudo del hot end (extendiendo el tubo de PTFE unos 20 mm).
### Para hotend M4
#### Pasos para cargar filamentos en el hotend M4:
##### (https://www.youtube.com/watch?v=-47yB95uIxI)
Al cargar los filamentos en el hotend M4, independientemente de cuántos extrusores necesite usar durante la impresión, ***los cuatro filamentos deben cargarse en el hotend***, y es importante ***asegurarse de que todos los filamentos estén cargado en la parte inferior del hotend*** antes de comenzar a imprimir.     
:warning: ***Ya sea que imprima en un solo color o en varios colores, debe cargar los cuatro filamentos en el hotend M4V6.***
1. Corta la parte frontal del filamento con unos alicates diagonales antes de cargarlo en el extrusor y el hotend.
2. Cargue 4 filamentos en todos los extrusores uno por uno y luego gire el engranaje de los extrusores hasta que el filamento entre en el tubo interior de PTFE del hotend, gire más de 4 a 5 vueltas y luego deténgase.

#### Pasos para descargar el filamento del hotend M4:
1. Calentar la boquilla (200 ℃ para PLA / 230 ℃ para PETG/ABS) y esperar a que alcance la temperatura ***Menu: Prepare>>Filament>>Preheat: 200/230***.
2. Alimente los filamentos al menos 10 mm en los 4 canales simultáneamente ***Menu: Prepare>>Filament>>Extruder: All; Prepare>>Filament>>Slowly Load***.
3. Descargue los filamentos del hotend ***Menu: Prepare>>Filament>>Slowly unload***.
  
### Para hotend E4
#### <a id = "PRELOAD_FILAMENT">Pasos para cargar filamentos en el hotend E4:</a>
##### (https://www.youtube.com/watch?v=FyHrAMytlT8)
Si comprende el principio de funcionamiento del hotend E4, ya debería saber que al imprimir en varios colores, la máquina primero debe descargar el filamento previamente cargado del hotend y luego cargar el siguiente filamento. Sin embargo, normalmente ***la máquina no tiene la capacidad de reconocer la distancia entre el extremo frontal del filamento y la boquilla antes de comenzar a imprimir***. Por lo tanto, necesitamos configurar un proceso llamado <u>***"filamentos de precarga"***</u>, cuyo objetivo es permitir que la máquina mueva los hilos finos a una posición adecuada conocida por la máquina antes. imprimiendo el objeto.
:warning: ***Solo los filamentos del extrusor que deben usarse en el archivo gcode deben cargarse en el hotend E4.***

### Pasos para descargar filamento del hotend E4:
1. Calentar la boquilla (200 ℃ para PLA / 230 ℃ para PETG/ABS). ***Menú: Preparar>>Filamento>>Precalentar: 200/230***
2. Alimente el filamento al menos 10 mm en el extrusor usado. ***Menú: Preparar>>Filamento>>Extruidor: 1/2/3/4; Preparar>>Filamento>>Cargar lentamente***
3. Descargue el filamento del fusor. ***Menú: Preparar>>Filamento>>Descargar lentamente***

-----
## <a id = "A4">¿Cuál es la diferencia en la configuración de corte entre el hotend M4 y E4?</a>
:pushpin: Estas configuraciones se han establecido en los perfiles del software PrusaSlicer que proporcionamos. Solo necesita elegir el **preajuste de impresora** correcto según su máquina y tipo de hotend.
### Configuración de corte para impresión multicolor
Para imprimir en varios colores, las configuraciones de corte para el hotend E4 y el hotend M4 difieren principalmente de la siguiente manera:
- **iniciar gcode**
   - **Para el hotend E4**, requiere "filamentos precargados" antes de comenzar a imprimir ([**Know Why**](#PRELOAD_FILAMENT)), para más detalles, consulte [**start gcode of the E4 hotend**][E4_STARTGCODE].
   - **Para el hotend M4**, al imprimir no más de 4 colores, no es necesario realizar cambios especiales en el gcode de inicio. Pero **si necesita imprimir más de 4 colores** (mezclando filamentos de diferentes colores en varios colores), puede configurar la proporción de mezcla de colores en el código de inicio. Para obtener más información, consulte [**Cómo imprimir más de 4 colores utilizando el extremo caliente M4**][M4_MIXMULTICOLORPRINT].
- **Configuración de retracción de los extrusores**
   - **Para el hotend E4**, la **Longitud de retracción** recomendada es de 6 ~ 8 mm (debe ser inferior a 10 mm).
   - **Para el hotend M4**, la **Longitud de retracción** recomendada es de 8 ~ 15 mm.
- **Torre de limpieza (Torre principal)**
:pushpin: El software de corte que admite múltiples impresoras extrusoras tiene una opción **"Wipe Tower(Prime Tower)"**. Porque cuando la impresora cambia de un extrusor a otro, a menudo necesita limpiar primero los hilos finos del color anterior en el extremo caliente. Después de activar la opción de borrado de la torre, el software de corte puede generar una impresión "adicional" en el archivo gcode para limpiar los filamentos restantes en el extremo caliente.
   - **Para el hotend E4**, el volumen requerido de la torre de cables es relativamente pequeño.
   - **Para el hotend M4**, el volumen requerido de la torre de cables es relativamente grande.
- **Código G de cambio de herramienta**
   - **Para el hotend E4**, al cambiar el extrusor, es necesario sacar el filamento del color anterior del hotend y luego cargar el filamento del siguiente color en el hotend. Por lo tanto, es necesario configurar Tool Change Gcode para lograr esta operación. Para obtener más información, consulte [**Código G de cambio de herramienta para hotend E4**][E4_TOOLCHANGE].
   - **Para el hotend M4**, no necesita **Código G de cambio de herramienta**.

-----
## <a id="A5">Cómo cambiar entre hotend M4 y hotend E4</a>
### 1. Afloje los tres tornillos de la carcasa del hotend y retire el hotend viejo de la máquina (x polea). Luego instale el nuevo hotend en la máquina (polea x) y bloquee los tornillos.

### 2. Conecte los cables del nuevo hotend a la máquina.
 
### 3. Configure el tipo de hotend en el menú LCD: *Control>>Configurar>>Tipo de hotend*

#### :pushpin: Los conectores del cabezal de impresión Z9V5 están ocultos dentro de la máquina, es necesario quitar el anillo de goma y sacar los conectores.

### :warning: NOTA 1: Si no puede encontrar el menú "tipo de hotend" en la pantalla LCD, cargue el firmware más reciente en su impresora.
[**:point_right: Firmware para Z9V5**][FW_Z9V5] / [**:point_right: Firmware para Z8P**][FW_Z8P] / [**:point_right: Firmware para Z9M4**][FW_Z9M4]
### :warning: NOTA 2: El hotend de colores mezclados y el hotend de colores no mezclados deben usar configuraciones de corte diferentes; preste atención para distinguirlos. Usar una configuración de corte incorrecta puede bloquear el hotend.

-----

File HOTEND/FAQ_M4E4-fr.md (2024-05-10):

[E4_STARTGCODE]: https://github.com/ZONESTAR3D/Slicing-Guide/blob/master/PrusaSlicer/Custom_Gcode.md#start-g-code
[M4_MIXMULTICOLORPRINT]: https://github.com/ZONESTAR3D/Slicing-Guide/blob/master/PrusaSlicer/PrusaSlicerGuide_M4.md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
[E4_TOOLCHANGE]: https://github.com/ZONESTAR3D/Slicing-Guide/blob/master/PrusaSlicer/Custom_Gcode.md#tool-change-g-code
[FW_Z9V5]: https://github.com/ZONESTAR3D/Firmware/tree/master/Z9/Z9V5/bin
[FW_Z9M4]: https://github.com/ZONESTAR3D/Firmware/tree/master/Z9/Z9M4
[FW_Z8P]: https://github.com/ZONESTAR3D/Firmware/tree/master/Z8/Z8P

----
## <a id="choose-language">:globe_with_meridians: Choose language </a>









<!-- [![](../lanpic/SA.png)](https://github.com/ZONESTAR3D/Upgrade-kit-guide/tree/main/HOTEND/FAQ_M4E4-ar.md) -->

----
# FAQ pour les hotend E4 et M4
- [**Quelle est la différence entre le hotend E4 et M4 ?**](#A1)
- [**Quel type de hotend dois-je choisir ?**](#A2)
- [**Comment charger correctement les filaments dans le hotend ?**](#A3)
- [**Quelle est la différence dans les paramètres de découpage entre les hotends M4 et E4**](#A4)
- [**Comment basculer entre le hotend M4 et E4 ?**](#A5)

-----
## <a id="A1">Quelle est la différence entre le hotend E4 et M4 ?</a>
   
- **M4 hotend** peut mélanger des filaments de différentes couleurs pour produire de nouveaux filaments colorés. **E4 hotend** n'a pas cette capacité.
- **E4 hotend** est efficace pour imprimer des objets 3D monochromes ou multicolores (jusqu'à 4 couleurs).
- **M4 hotend** est bon pour imprimer des objets 3D en dégradé de couleurs, il peut également imprimer plus de 4 objets 3D colos (en mélangeant les filaments).
### Principe de fonctionnement du hotend E4

### Principe de fonctionnement du hotend M4
[](https://github.com/ZONESTAR3D/Document-and-User-Guide/assets/29502731/2b9f4d75-b6fd-486f-aaa7-7a1163383316)

### Avantages du hotend E4
1. Une « tour principale de commutateur d'extrudeuse » plus petite lors de l'impression d'un objet 3D multicolore.
2. Meilleure qualité lors de l’impression d’un objet 3D d’une seule couleur.
3. Prise en charge de l'impression de différents types de filaments sur le même objet 3D.
### Avantages du hotend M4
1. Prend en charge le mélange de filaments de différentes couleurs avec de nouvelles couleurs.
2. Prise en charge de l'impression de couleurs dégradées.
3. Supporte un débit plus élevé.


-----
## <a id="A2"> Quel hotend dois-je choisir, M4 ou E4 ?</a>
- Si vous **n'avez pas besoin** d'imprimer un modèle 3D en dégradé de couleurs, nous vous suggérons de choisir **E4 hotend**, il peut obtenir une meilleure qualité d'impression d'impressions 3D monochromes et multicolores.
- Si vous souhaitez imprimer un modèle 3D **dégradé de couleur**, ou si vous souhaitez **mélanger des filaments de différentes couleurs avec une autre couleur**, choisissez le hotend M4.

-----
## <a id="A3"> Comment charger/décharger correctement les filaments</a>
L'extrémité chaude M4 et l'extrémité chaude E4 ont des exigences différentes pour le chargement du filament.
- **Exigences de quantité pour le chargement des filaments :**
   - L'extrémité chaude M4 nécessite le chargement de quatre filaments en même temps, qu'il s'agisse d'une impression monochrome ou multicolore ;
   - Le hot end E4 peut choisir le nombre de filaments à charger en fonction des couleurs imprimées.
- **Exigences de position pour le chargement des filaments :**
   - Le hot end M4 nécessite que le filament soit installé au bas du hot end ;
   - Le hot end E4 nécessite que le filament soit installé au-dessus de l'embouchure de l'entonnoir du hot end (en prolongeant le tube PTFE d'environ 20 mm).
### Pour M4 Hotend
#### Étapes pour charger les filaments dans le hotend M4 :
##### (https://www.youtube.com/watch?v=-47yB95uIxI)
Lors du chargement des filaments dans le hotend M4, quel que soit le nombre d'extrudeuses que vous devez utiliser pendant l'impression, ***les quatre filaments doivent être chargés dans le hotend***, et il est important de ***s'assurer que tous les filaments sont chargé au bas du hotend*** avant de commencer l'impression.    
:warning: ***Que vous imprimiez en monochrome ou en multicolore, vous devez charger les quatre filaments dans le hotend M4V6.***
1. Coupez l'avant du filament avec une pince diagonale avant de le charger dans l'extrudeuse et la hotend.
2. Chargez 4 filaments dans toutes les extrudeuses un par un, puis faites tourner l'engrenage des extrudeuses jusqu'à ce que le filament entre dans le tube PTFE intérieur du hotend, faites tourner encore 4 à 5 tours, puis arrêtez-vous.

#### Étapes pour décharger le filament du hotend M4 :
1. Chauffez la buse (200℃ pour PLA / 230℃ pour PETG/ABS) et attendez que la température atteigne. ***Menu: Prepare>>Filament>>Preheat: 200/230***.
2. Alimentez les filaments sur au moins 10 mm sur les 4 canaux simultanément ***Menu: Prepare>>Filament>>Extruder: All; Prepare>>Filament>>Slowly Load***.
3. Déchargez les filaments du hotend ***Menu: Prepare>>Filament>>Slowly unload***.
  
### Pour E4 Hotend
#### <a id = "PRELOAD_FILAMENT">Étapes pour charger les filaments dans la hotend E4:</a>
##### (https://www.youtube.com/watch?v=FyHrAMytlT8)
Si vous comprenez le principe de fonctionnement du hotend E4, sachez déjà que lors d'une impression multicolore, la machine doit d'abord décharger le filament précédemment chargé du hotend, puis charger le filament suivant. Cependant, généralement ***la machine n'a pas la capacité de reconnaître la distance entre l'extrémité avant du filament et la buse avant de commencer l'impression***. Il faut donc mettre en place un procédé appelé <u>***"précharge filaments"***</u>, qui a pour but de permettre à la machine de déplacer les fils fins vers une position adaptée connue de la machine avant imprimer l'objet.
:warning: ***Seuls les filaments de l'extrudeuse qui doivent être utilisés dans le fichier gcode doivent être chargés dans le hotend E4.***

### Étapes pour décharger le filament du hotend E4:
1. Chauffer la buse (200℃ pour PLA / 230℃ pour PETG/ABS) et attendez que la température atteigne. ***Menu: Prepare>>Filament>>Preheat: 200/230***
2. Alimentez le filament sur au moins 10 mm sur l'extrudeuse utilisée. ***Menu: Prepare>>Filament>>Extruder: 1/2/3/4; Prepare>>Filament>>Slowly Load***
3. Déchargez le filament de la hotend. ***Menu: Prepare>>Filament>>Slowly unload***

-----
## <a id = "A4">Quelle est la différence dans les paramètres de découpage entre les hotend M4 et E4:</a>
:pushpin: Ces paramètres ont été définis dans les profils du logiciel PrusaSlicer que nous fournissons. Il vous suffit de choisir le bon **préréglage d'imprimante** en fonction de votre machine et du type de hotend.
### Paramètres de tranche pour l'impression multicolore
Pour l'impression multicolore, les paramètres de découpage pour le hotend E4 et le hotend M4 diffèrent principalement comme suit:
- **démarrer gcode**
   - **Pour le hotend E4**, il faut "précharger les filaments" avant de commencer l'impression ([**Know Why**](#PRELOAD_FILAMENT)), pour plus de détails, veuillez vous référer au [**start gcode de l'E4 hotend**][E4_STARTGCODE].
   - **Pour le hotend M4**, lors de l'impression de 4 couleurs maximum, il n'est pas nécessaire d'apporter des modifications particulières au gcode de démarrage. Mais **si vous devez imprimer plus de 4 couleurs** (en mélangeant des filaments de différentes couleurs en plusieurs couleurs), vous pouvez définir le rapport de mélange des couleurs dans le gcode de démarrage. Pour plus de détails, veuillez vous référer à [**Comment imprimer plus de 4 couleurs à l'aide du hot end M4**][M4_MIXMULTICOLORPRINT].
- **Paramètres de rétraction des extrudeuses**
   - **Pour le hotend E4**, la **longueur de rétraction** recommandée est de 6 à 8 mm (doit être inférieure à 10 mm).
   - **Pour le hotend M4**, la **longueur de rétraction** recommandée est de 8 à 15 mm.
- **Tour d'essuyage (Tour Prime)**
:pushpin: Le logiciel de découpage qui prend en charge plusieurs imprimantes extrudeuses dispose d'une option **"Wipe Tower (Prime Tower)"**. Car lorsque l’imprimante passe d’une extrudeuse à une autre, elle doit souvent d’abord nettoyer les fils fins de la couleur précédente dans la partie chaude. Après avoir activé l'option d'effacement de la tour, le logiciel de découpage peut générer une impression « supplémentaire » dans le fichier gcode pour nettoyer les filaments restants dans l'extrémité chaude.
   - **Pour le hotend E4**, le volume requis de la tour filaire est relativement faible.
   - **Pour le hotend M4**, le volume requis de la tour filaire est relativement important.
- **Changement d'outil G-code**
   - **Pour le hotend E4**, lors du changement d'extrudeuse, il est nécessaire de retirer le filament de couleur précédent du hotend puis de charger le filament de couleur suivant dans le hotend. Par conséquent, Tool Change Gcode doit être défini pour réaliser cette opération. Pour plus de détails, veuillez vous référer à [**Tool change G-code for E4 hotend**][E4_TOOLCHANGE].
   - **Pour le hotend M4**, il n'a pas besoin de **outil de changement de G-code**.

-----
## <a id="A5"> Comment basculer entre le hotend M4 et le hotend E4</a>
### 1. Desserrez les trois vis du boîtier du hotend et retirez l'ancien hotend de la machine (x poulie). Installez ensuite le nouveau hotend sur la machine (x poulie) et verrouillez les vis.

### 2. Connectez les fils du nouveau hotend à la machine.
 
### 3. Définissez le type de hotend sur le menu LCD : *Contrôle>>Configurer>>Type de hotend*

#### :pushpin: Les connecteurs de la tête d'impression Z9V5 sont cachés à l'intérieur de la machine, vous devez retirer l'anneau en caoutchouc et retirer les connecteurs.

### :warning: REMARQUE 1: Si vous ne trouvez pas le menu « type de hotend » sur l'écran LCD, veuillez télécharger le micrologiciel le plus récent sur votre imprimante.
[**:point_right: Firmware pour Z9V5**][FW_Z9V5] / [**:point_right: Firmware pour Z8P**][FW_Z8P] / [**:point_right: Firmware pour Z9M4**][FW_Z9M4]
### :warning: REMARQUE 2: le Hotend de couleurs mélangées et le hotend de couleurs non mélangées doivent utiliser des paramètres de tranche différents, veuillez faire attention à la distinction. L’utilisation d’un mauvais réglage de tranche peut bloquer le hotend.

-----

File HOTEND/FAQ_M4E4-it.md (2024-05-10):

[E4_STARTGCODE]: https://github.com/ZONESTAR3D/Slicing-Guide/blob/master/PrusaSlicer/Custom_Gcode.md#start-g-code
[M4_MIXMULTICOLORPRINT]: https://github.com/ZONESTAR3D/Slicing-Guide/blob/master/PrusaSlicer/PrusaSlicerGuide_M4.md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
[E4_TOOLCHANGE]: https://github.com/ZONESTAR3D/Slicing-Guide/blob/master/PrusaSlicer/Custom_Gcode.md#tool-change-g-code
[FW_Z9V5]: https://github.com/ZONESTAR3D/Firmware/tree/master/Z9/Z9V5/bin
[FW_Z9M4]: https://github.com/ZONESTAR3D/Firmware/tree/master/Z9/Z9M4
[FW_Z8P]: https://github.com/ZONESTAR3D/Firmware/tree/master/Z8/Z8P

----
## <a id="choose-language">:globe_with_meridians: Choose language </a>









<!-- [![](../lanpic/SA.png)](https://github.com/ZONESTAR3D/Upgrade-kit-guide/tree/main/HOTEND/FAQ_M4E4-ar.md) -->

----
# FAQ per hotend E4 e M4
- [**Qual è la differenza tra l'hotend E4 e M4?**](#A1)
- [**Che tipo di hotend dovrei scegliere?**](#A2)
- [**Come caricare correttamente i filamenti nell'hotend?**](#A3)
- [**Qual è la differenza nelle impostazioni di slicing tra gli hotend M4 ed E4**](#A4)
- [**Come passare dall'hotend M4 all'hotend E4?**](#A5)

-----
## <a id="A1">Cosa c'è di diverso tra l'hotend E4 e M4?</a>
   
- **Hotend M4** può mescolare diversi filamenti colorati per produrre nuovi filamenti colorati. **Hotend E4** non ha questa capacità.
- **Hotend E4** è ottimo per stampare oggetti 3D monocolore o multicolori (fino a 4 colori).
- **M4 hotend** è ottimo per stampare oggetti 3D a colori sfumati, può anche stampare più di 4 oggetti 3D a colori (mescolando i filamenti).
### Principio di funzionamento dell'hotend E4

### Principio di funzionamento dell'hotend M4
[](https://github.com/ZONESTAR3D/Document-and-User-Guide/assets/29502731/2b9f4d75-b6fd-486f-aaa7-7a1163383316)

### Vantaggi dell'hotend E4
1. "Torre principale dell'interruttore estrusore" più piccola durante la stampa di oggetti 3D multicolori.
2. Migliore qualità durante la stampa di oggetti 3D a un colore.
3. Supporto per stampare diversi tipi di filamento sullo stesso oggetto 3D.
### Vantaggi dell'hotend M4
1. Supporta la miscelazione di filamenti di colore diverso con nuovi colori.
2. Supporta la stampa a colori sfumati.
3. Supporta una portata più elevata.


-----
## <a id="A2"> Quale hotend dovrei scegliere, M4 o E4?</a>
- Se **non hai bisogno** di stampare un modello 3D a colori sfumati, ti consigliamo di scegliere **hotend E4**, può ottenere una qualità migliore nella stampa di stampe 3D monocolore e multicolori.
- Se desideri stampare un modello 3D di **colore sfumato** o vuoi **mescolare filamenti di colore diverso in un altro colore**, scegli l'hotend M4.

-----
## <a id="A3"> Come caricare/scaricare correttamente i filamenti</a>
L'hotend M4 e l'hotend E4 hanno requisiti diversi per il caricamento del filamento.
- **Requisiti di quantità per caricare i filamenti:**
   - L'hot end M4 richiede il caricamento di quattro filamenti contemporaneamente, indipendentemente dal fatto che si stampi monocolore o multicolore;
   - L'hot end E4 può scegliere il numero di filamenti da caricare in base ai colori stampati.
- **Requisiti di posizione per il caricamento dei filamenti:**
   - L'hot end M4 richiede che il filamento sia installato nella parte inferiore dell'hot end;
   - L'hot end E4 richiede che il filamento sia installato sopra la bocca dell'imbuto dell'hot end (estendendo il tubo PTFE di circa 20 mm).
### Per l'hotend M4
#### Passaggi per caricare i filamenti nell'hotend M4:
##### (https://www.youtube.com/watch?v=-47yB95uIxI)
Quando si caricano i filamenti nell'hotend M4, indipendentemente dal numero di estrusori necessari durante la stampa, ***tutti e quattro i filamenti devono essere caricati nell'hotend*** ed è importante ***assicurarsi che tutti i filamenti siano caricato nella parte inferiore dell'hotend*** prima di iniziare la stampa.
:warning: ***Che si stampi in monocolore o multicolore, è necessario caricare tutti e quattro i filamenti nell'hotend M4V6.***
1. Taglia la parte anteriore del filamento con una pinza diagonale prima di caricarlo nell'estrusore e nell'hotend.
2. Caricare 4 filamenti su tutti gli estrusori uno per uno, quindi ruotare l'ingranaggio degli estrusori finché il filamento non entra nel tubo interno in PTFE dell'hotend, ruotare di altri 4 ~ 5 giri e poi fermarsi.

#### Passaggi per scaricare il filamento dall'hotend M4:
1. Riscaldare l'ugello (200℃ per PLA / 230℃ per PETG/ABS) e attendere che venga raggiunta la temperatura. ***Menu: Prepare>>Filament>>Preheat: 200/230***
2. Alimentare i filamenti per almeno 10 mm su tutti e 4 i canali contemporaneamente ***Menu: Prepare>>Filament>>Extruder: All; Prepare>>Filament>>Slowly Load***
3. Scaricare i filamenti dall'hotend ***Menu: Prepare>>Filament>>Slowly unload***.
  
### Per l'hotend E4
#### <a id = "PRELOAD_FILAMENT">Passaggi per caricare i filamenti nell'hotend E4:</a>
##### (https://www.youtube.com/watch?v=FyHrAMytlT8)
Se comprendi il principio di funzionamento dell'hotend E4, dovresti già sapere che quando si stampa multicolore, la macchina deve prima scaricare il filamento precedentemente caricato dall'hotend e poi caricare il filamento successivo. Tuttavia, solitamente ***la macchina non ha la capacità di riconoscere la distanza tra l'estremità anteriore del filamento e l'ugello prima di iniziare la stampa***. Pertanto, dobbiamo impostare un processo chiamato <u>***"precarica filamenti"***</u>, che mira a consentire alla macchina di spostare i fili sottili in una posizione adatta nota alla macchina prima stampare l'oggetto.
:warning: ***Solo i filamenti sull'estrusore che devono essere utilizzati nel file gcode devono essere caricati nell'hotend E4.***

### Passaggi per scaricare il filamento dall'hotend E4:
1. Riscaldamento dell'ugello (200℃ per PLA/230℃ per PETG/ABS) e attendere che venga raggiunta la temperatura. ***Menu: Prepare>>Filament>>Preheat: 200/230***
2. Alimentare il filamento per almeno 10 mm sull'estrusore usato. ***Menu: Prepare>>Filament>>Extruder: 1/2/3/4; Prepare>>Filament>>Slowly Load***
3. Scarica il filamento dall'hotend. ***Menu: Prepare>>Filament>>Slowly unload***

-----
## <a id = "A4">Qual è la differenza nelle impostazioni di slicing tra l'hotend M4 e E4:</a>
:pushpin: Queste impostazioni sono state configurate nei profili del software PrusaSlicer che forniamo. Devi solo scegliere la **preimpostazione della stampante** corretta in base alla tua macchina e al tipo di hotend.
### Impostazioni delle sezioni per la stampa multicolore
Per la stampa multicolore, le impostazioni di suddivisione per l'hotend E4 e l'hotend M4 differiscono principalmente come segue:
- **avvia gcode**
   - **Per l'hotend E4**, è necessario "precaricare i filamenti" prima di iniziare la stampa([**Know Why**](#PRELOAD_FILAMENT)), per i dettagli, fare riferimento a [**start gcode dell'E4 hotend**][E4_STARTGCODE].
   - **Per l'hotend M4**, quando si stampa non più di 4 colori, non è necessario apportare modifiche speciali al gcode iniziale. Ma **se devi stampare più di 4 colori** (mescolando filamenti colorati diversi in più colori), puoi impostare il rapporto di miscelazione dei colori nel gcode iniziale. Per i dettagli, fare riferimento a [**Come stampare più di 4 colori utilizzando l'hot end M4**][M4_MIXMULTICOLORPRINT].
- **Impostazioni di retrazione degli estrusori**
   - **Per l'hotend E4**, la **Lunghezza di retrazione** consigliata è 6 ~ 8 mm (deve essere inferiore a 10 mm).
   - **Per l'hotend M4**, la **Lunghezza di retrazione** consigliata è 8 ~ 15 mm.
- **Torre di pulizia (Torre Prime)**
:pushpin: Il software di slicing che supporta più stampanti con estrusore ha un'opzione **"Wipe Tower(Prime Tower)"**. Perché quando la stampante passa da un estrusore all'altro, spesso ha bisogno prima di pulire i fili sottili del colore precedente nell'hot end. Dopo aver attivato l'opzione di cancellazione della torre, il software di slicing può generare una stampa "aggiuntiva" nel file gcode per ripulire eventuali filamenti rimanenti nell'hot end.
   - **Per l'hotend E4**, il volume richiesto della torre di cablaggio è relativamente piccolo.
   - **Per l'hotend M4**, il volume richiesto della torre di cablaggio è relativamente grande.
- **Codice G cambio utensile**
   - **Per l'hotend E4**, quando si cambia l'estrusore, è necessario estrarre il filamento di colore precedente dall'hotend e quindi caricare il filamento di colore successivo nell'hotend. Pertanto, per eseguire questa operazione è necessario impostare il Gcode cambio utensile. Per i dettagli, fare riferimento a [**Codice G cambio utensile per hotend E4**][E4_TOOLCHANGE].
   - **Per l'hotend M4**, non è necessario il **codice G per il cambio utensile**.

-----
## <a id="A5"> Come passare dall'hotend M4 all'hotend E4</a>
### 1. Allenta le tre viti sull'alloggiamento dell'hotend e rimuovi il vecchio hotend dalla macchina (x puleggia). Quindi installare il nuovo hotend sulla macchina (x puleggia) e bloccare le viti.

### 2. Collega i cavi del nuovo hotend alla macchina.
 
### 3. Imposta il tipo di hotend sul menu LCD: *Controllo>>Configura>>Tipo di hotend*

#### :pushpin: I connettori della testina di stampa Z9V5 sono nascosti all'interno della macchina, è necessario rimuovere l'anello di gomma ed estrarre i connettori.

### :warning: NOTA 1: Se non riesci a trovare il menu "tipo hotend" sullo schermo LCD, carica il firmware più recente sulla tua stampante.
[**:point_right: firmware per Z9V5**][FW_Z9V5] / [**:point_right: firmware per Z8P**][FW_Z8P] / [**:point_right: firmware per Z9M4**][FW_Z9M4]
### :warning: NOTA 2: L'hotend a colori misti e l'hotend a colori non misti devono utilizzare impostazioni di sezione diverse, prestare attenzione a distinguere. L'utilizzo dell'impostazione errata della sezione potrebbe bloccare l'hotend.

-----

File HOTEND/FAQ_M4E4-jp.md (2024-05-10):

[E4_STARTGCODE]: https://github.com/ZONESTAR3D/Slicing-Guide/blob/master/PrusaSlicer/Custom_Gcode.md#start-g-code
[M4_MIXMULTICOLORPRINT]: https://github.com/ZONESTAR3D/Slicing-Guide/blob/master/PrusaSlicer/PrusaSlicerGuide_M4.md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
[E4_TOOLCHANGE]: https://github.com/ZONESTAR3D/Slicing-Guide/blob/master/PrusaSlicer/Custom_Gcode.md#tool-change-g-code
[FW_Z9V5]: https://github.com/ZONESTAR3D/Firmware/tree/master/Z9/Z9V5/bin
[FW_Z9M4]: https://github.com/ZONESTAR3D/Firmware/tree/master/Z9/Z9M4
[FW_Z8P]: https://github.com/ZONESTAR3D/Firmware/tree/master/Z8/Z8P

----
## <a id="choose-language">:globe_with_meridians: Choose language </a>









<!-- [![](../lanpic/SA.png)](https://github.com/ZONESTAR3D/Upgrade-kit-guide/tree/main/HOTEND/FAQ_M4E4-ar.md) -->

----
# E4 および M4 ホットエンドに関する FAQ
- [**E4 ホットエンドと M4 ホットエンドの違いは何ですか?**](#A1)
- [**どのタイプのホットエンドを選択すればよいですか?**](#A2)
- [**フィラメントをホットエンドに正しくロードするにはどうすればよいですか?**](#A3)
- [**M4 ホットエンドと E4 ホットエンドのスライス設定の違いは何ですか**](#A4)
- [**M4 と E4 ホットエンドを切り替えるにはどうすればよいですか?**](#A5)

-----
## <a id="A1">E4 ホットエンドと M4 ホットエンドの違いは何ですか?</a>
   
- **M4 ホットエンド** は、異なる色のフィラメントを混合して新しい色のフィラメントを生成できます。 **E4 ホットエンド** にはこの機能がありません。
- **E4 ホットエンド** は、1 色または複数色の 3D オブジェクト (最大 4 色) の印刷に優れています。
- **M4 ホットエンド** は、グラデーション カラー 3D オブジェクトの印刷に優れており、(フィラメントを混合することにより) 4 色以上の 3D オブジェクトも印刷できます。
### E4 ホットエンドの動作原理

### M4 ホットエンドの動作原理
[](https://github.com/ZONESTAR3D/Document-and-User-Guide/assets/29502731/2b9f4d75-b6fd-486f-aaa7-7a1163383316)

### E4 ホットエンドの利点
1. マルチカラー 3D オブジェクトを印刷する際の「エクストルーダー スイッチ プライム タワー」を小型化。
2. 1 色の 3D オブジェクトを印刷する場合の品質が向上します。
3. 同じ 3D オブジェクト上に異なるタイプのフィラメントを印刷することをサポートします。
### M4 ホットエンドの利点
1. 異なる色のフィラメントを混合して新しい色を作成することをサポートします。
2. グラデーションカラー印刷をサポートします。
3. より高い流量をサポートします。


-----
## <a id="A2"> M4 と E4 のどちらのホットエンドを選択すればよいですか?</a>
- グラデーション カラー 3D モデルを印刷する**必要がない**場合は、**E4 ホットエンド**を選択することをお勧めします。これにより、単色およびマルチカラー 3D プリントの印刷品質が向上します。
- **グラデーション カラー** 3D モデルを印刷する場合、または **異なる色のフィラメントを別の色に混合する**場合は、M4 ホットエンドを選択します。

-----
## <a id="A3"> フィラメントを正しくロード/アンロードする方法</a>  
M4 ホットエンドと E4 ホットエンドには、フィラメントの装着に関する要件が異なります。     
- **フィラメントを装填するための数量の要件:**    
   - M4 ホットエンドでは、単色印刷か多色印刷かに関係なく、同時に 4 本のフィラメントをロードする必要があります。
   - E4 ホットエンドは、印刷する色に応じてロードするフィラメントの数を選択できます。
- **フィラメントを装填する位置の要件:**
   - M4 ホットエンドでは、フィラメントをホットエンドの底部に取り付ける必要があります。
   - E4 ホットエンドでは、フィラメントをホットエンドの漏斗口の上に取り付ける必要があります (PTFE チューブを約 20mm 延長します)。
### M4 ホットエンド用
#### M4 ホットエンドにフィラメントをロードする手順:
##### (https://www.youtube.com/watch?v=-47yB95uIxI)
フィラメントを M4 ホットエンドにロードするときは、印刷中に使用する必要がある押出機の数に関係なく、***4 つのフィラメントすべてをホットエンドにロードする必要があります***。また、**すべてのフィラメントが確実にロードされていることを確認することが重要です。印刷を開始する前にホットエンド***の下部にロードされます。     
:warning: ***単色で印刷する場合でも、マルチカラーで印刷する場合でも、4 本のフィラメントすべてを M4V6 ホットエンドにロードする必要があります。***       
1. エクストルーダーとホットエンドにロードする前に、フィラメントの前面を斜めペンチでカットします。
2. 4 本のフィラメントをすべてのエクストルーダーに 1 本ずつロードし、フィラメントがホットエンドの内側 PTFE チューブに入るまでエクストルーダーのギアを回転させ、さらに 4 ～ 5 回転回転させて停止します。

#### M4 ホットエンドからフィラメントをアンロードする手順:
1. ノズルを加熱し (PLA の場合は 200℃ / PETG/ABS の場合は 230℃)、その温度に達するまで待ちます。 ***Menu: Prepare>>Filament>>Preheat: 200/230***
2. 4 つのチャンネルすべてに同時にフィラメントを少なくとも 10 mm 供給します。***Menu: Prepare>>Filament>>Extruder: All; Prepare>>Filament>>Slowly Load***。
3. ホットエンドからフィラメントをアンロードします。***Menu: Prepare>>Filament>>Slowly unload***。
  
### E4 ホットエンド用
#### <a id = "PRELOAD_FILAMENT">E4 ホットエンドにフィラメントをロードする手順:</a>
##### (https://www.youtube.com/watch?v=FyHrAMytlT8)
E4 ホットエンドの動作原理を理解している場合は、マルチカラーを印刷する場合、マシンはまず以前にロードされたフィラメントをホットエンドからアンロードし、次に次のフィラメントをロードする必要があることをすでに知っているはずです。 ただし、通常、**機械には印刷を開始する前にフィラメントの先端とノズルの間の距離を認識する機能がありません***。 したがって、<u>***「フィラメントのプリロード」***</u> と呼ばれるプロセスをセットアップする必要があります。これは、機械が事前に知っている適切な位置に細い糸を移動できるようにすることを目的としています。 オブジェクトを印刷します。     
:warning: ***gcode ファイルで使用する必要があるエクストルーダーのフィラメントのみを E4 ホットエンドにロードする必要があります。***

### E4 ホットエンドからフィラメントをアンロードする手順:
1. ノズルを加熱し (PLA の場合は 200℃ / PETG/ABS の場合は 230℃)、その温度に達するまで待ちます。 ***Menu: Prepare>>Filament>>Preheat: 200/230***
2. 使用済みエクストルーダーにフィラメントを少なくとも 10mm 供給します。 ***Menu: Prepare>>Filament>>Extruder: 1/2/3/4; Prepare>>Filament>>Slowly Load***.
3. フィラメントをホットエンドからアンロードします。 ***Menu: Prepare>>Filament>>Slowly unload***

-----
## <a id = "A4">M4 ホットエンドと E4 ホットエンドのスライス設定の違いは何ですか:</a>
:pushpin: これらの設定は、当社が提供する PrusaSlicer ソフトウェアのプロファイルに設定されています。 必要なのは、お使いのマシンとホットエンドのタイプに応じて正しい **プリンター プリセット** を選択することだけです。
### 多色印刷のスライス設定
マルチカラー印刷の場合、E4 ホットエンドと M4 ホットエンドのスライス設定は主に次のように異なります。
- **gcode を開始**
   - **E4 ホットエンド**の場合、印刷を開始する前に「フィラメントのプリロード」が必要です ([**Know Why**](#PRELOAD_FILAMENT))。詳細については、[**E4 ホットエンドの gcode の開始**][E4_STARTGCODE] を参照してください。
   - **M4 ホットエンド**の場合、4 色以下を印刷する場合、開始 gcode に特別な変更を加える必要はありません。 ただし、**4 色以上を印刷する必要がある** (異なる色のフィラメントを複数の色に混合する) 場合は、開始 gcode で色の混合比を設定できます。 詳細については、[**M4 ホットエンドを使用して 4 色以上の色を印刷する方法**][M4_MIXMULTICOLORPRINT]を参照してください。
- **エクストルーダーのリトラクション設定**
   - **E4 ホットエンド**の場合、推奨される**後退長**は 6 ～ 8mm (10mm 未満である必要があります) です。
   - **M4 ホットエンド**の場合、推奨**後退長**は 8 ～ 15mm です。
- **ワイプタワー（プライムタワー）**
:pushpin: 複数のエクストルーダープリンターをサポートするスライシングソフトウェアには、**「ワイプタワー(プライムタワー)」** オプションがあります。 なぜなら、プリンターがある押出機から別の押出機に切り替えるとき、多くの場合、最初にホットエンドにある前の色の細い糸をクリーニングする必要があるからです。 タワー消去オプションをオンにすると、スライシング ソフトウェアは gcode ファイルに「追加」プリントを生成し、ホット エンドに残っているフィラメントをクリーンアップします。
   - **E4 ホットエンド**の場合、必要なワイヤ タワーの体積は比較的小さくなります。
   - **M4 ホットエンド**の場合、必要なワイヤー タワーの体積は比較的大きくなります。
- **ツール交換 G コード**
   - **E4 ホットエンド**の場合、エクストルーダーを切り替えるときに、前の色のフィラメントをホットエンドから引き出し、次の色のフィラメントをホットエンドにロードする必要があります。 したがって、この操作を実現するにはツールチェンジ Gcode を設定する必要があります。 詳細については、[**E4 ホットエンド用ツール変更 G コード**][E4_TOOLCHANGE] を参照してください。
   - **M4 ホットエンド**の場合、**ツール変更 G コード**は必要ありません。

-----
## <a id="A5"> M4 ホットエンドと E4 ホットエンドを切り替える方法</a>
### 1. ホットエンド ハウジングの 3 本のネジを緩め、古いホットエンドをマシン (X プーリー) から取り外します。 次に、新しいホットエンドを機械 (X プーリー) に取り付け、ネジをロックします。

### 2. 新しいホットエンドのワイヤをマシンに接続します。
 
### 3. LCD メニューでホットエンド タイプを設定します: *Control>>Configure>>Hotend Type*

#### :pushpin: Z9V5 プリントヘッドのコネクタは機械の内部に隠されているため、ゴムリングを取り外してコネクタを引き抜く必要があります。

### :warning: 注 1: LCD 画面に「ホットエンド タイプ」メニューが見つからない場合は、最新のファームウェアをプリンタにアップロードしてください。
[**:point_right: Z9V5 用ファームウェア**][FW_Z9V5] / [**:point_right: Z8P 用ファームウェア**][FW_Z8P] / [**:point_right: Z9M4 用ファームウェア**][FW_Z9M4]
### :warning: 注 2: ミックス カラー ホットエンドと非ミックス カラー ホットエンドは異なるスライス設定を使用する必要があります。区別するように注意してください。 間違ったスライス設定を使用すると、ホットエンドがブロックされる可能性があります。

-----

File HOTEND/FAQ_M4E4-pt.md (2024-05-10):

[E4_STARTGCODE]: https://github.com/ZONESTAR3D/Slicing-Guide/blob/master/PrusaSlicer/Custom_Gcode.md#start-g-code
[M4_MIXMULTICOLORPRINT]: https://github.com/ZONESTAR3D/Slicing-Guide/blob/master/PrusaSlicer/PrusaSlicerGuide_M4.md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
[E4_TOOLCHANGE]: https://github.com/ZONESTAR3D/Slicing-Guide/blob/master/PrusaSlicer/Custom_Gcode.md#tool-change-g-code
[FW_Z9V5]: https://github.com/ZONESTAR3D/Firmware/tree/master/Z9/Z9V5/bin
[FW_Z9M4]: https://github.com/ZONESTAR3D/Firmware/tree/master/Z9/Z9M4
[FW_Z8P]: https://github.com/ZONESTAR3D/Firmware/tree/master/Z8/Z8P

----
## <a id="choose-language">:globe_with_meridians: Choose language </a>









<!-- [![](../lanpic/SA.png)](https://github.com/ZONESTAR3D/Upgrade-kit-guide/tree/main/HOTEND/FAQ_M4E4-ar.md) -->

----
# FAQ para hotend E4 e M4
- [**Qual é a diferença entre hotend E4 e M4?**](#A1)
- [**Que tipo de hotend devo escolher?**](#A2)
- [**Como carregar filamentos no hotend corretamente?**](#A3)
- [**Qual é a diferença nas configurações de fatiamento entre hotends M4 e E4**](#A4)
- [**Como alternar entre hotend M4 e E4?**](#A5)

-----
## <a id="A1">Qual é a diferença entre os hotends E4 e M4?</a>
   
- **M4 hotend** pode misturar filamentos de cores diferentes para produzir novos filamentos coloridos. **hotend E4** não tem essa capacidade.
- **E4 hotend** é bom para imprimir objetos 3D de uma ou várias cores (até 4 cores).
- **M4 hotend** é bom para imprimir objetos 3D em cores gradientes, ele também pode imprimir mais de 4 cores de objetos 3D (misturando os filamentos).
### Princípio de funcionamento do hotend E4

### Princípio de funcionamento do hotend M4
[](https://github.com/ZONESTAR3D/Document-and-User-Guide/assets/29502731/2b9f4d75-b6fd-486f-aaa7-7a1163383316)

### Vantagens do hotend E4
1. "Torre principal do interruptor da extrusora" menor durante a impressão de objetos 3D multicoloridos.
2. Melhor qualidade ao imprimir um objeto 3D colorido.
3. Suporte para imprimir diferentes tipos de filamento no mesmo objeto 3D.
### Vantagens do hotend M4
1. Suporte para misturar filamentos de cores diferentes com novas cores.
2. Suporte para impressão em cores gradientes.
3. Suporta maior taxa de fluxo.


-----
## <a id="A2"> Qual hotend devo escolher, M4 ou E4?</a>
- Se você **não precisa** imprimir o modelo 3D em cores gradientes, sugerimos que você escolha **E4 hotend**, ele pode obter melhor qualidade na impressão de impressões 3D em cores únicas e multicoloridas.
- Se você deseja imprimir modelo 3D de **cor gradiente** ou deseja **misturar filamentos de cores diferentes com outra cor**, escolha hotend M4.

-----
## <a id="A3"> Como carregar/descarregar filamentos corretamente</a>
O hot end M4 e o hot end E4 têm requisitos diferentes para carregar o filamento.
- **Requisitos de quantidade para carregamento de filamentos:**
   - O hot end M4 requer o carregamento de quatro filamentos ao mesmo tempo, independentemente de imprimir em uma cor ou multicolor;
   - O hot end E4 pode escolher a quantidade de filamentos a carregar de acordo com as cores impressas.
- **Requisitos de posição para carregamento de filamentos:**
   - O hot end M4 exige que o filamento seja instalado na parte inferior do hot end;
   - O hot end E4 requer que o filamento seja instalado acima da boca do funil do hot end (estendendo o tubo de PTFE em cerca de 20 mm).
### Para Hotend M4
#### Etapas para carregar filamentos no hotend M4:
##### (https://www.youtube.com/watch?v=-47yB95uIxI)
Ao carregar os filamentos no hotend M4, independentemente de quantas extrusoras você precisa usar durante a impressão, ***todos os quatro filamentos devem ser carregados no hotend***, e é importante ***garantir que todos os filamentos estejam carregado na parte inferior do hotend*** antes de iniciar a impressão.    
:warning: ***Seja imprimindo em uma única cor ou em várias cores, você precisa carregar todos os quatro filamentos no hotend M4V6.***
1. Corte a frente do filamento com um alicate diagonal antes de carregá-lo na extrusora e no hotend.    
2. Carregue 4 filamentos em todas as extrusoras, um por um, e depois gire a engrenagem das extrusoras até que o filamento entre no tubo interno de PTFE do hotend, gire mais 4 ~ 5 voltas e depois pare.

#### Passos para descarregar o filamento do hotend M4:
1. Aqueça o bico (200°C para PLA / 230°C para PETG/ABS) e aguarde a temperatura atingir ***Menu: Prepare>>Filament>>Preheat: 200/230***.
2. Alimente os filamentos pelo menos 10 mm em todos os 4 canais simultaneamente ***Menu: Prepare>>Filament>>Extruder: All; Prepare>>Filament>>Slowly Load***.
3. Descarregue os filamentos do hotend ***Menu: Prepare>>Filament>>Slowly unload***.
  
### Para Hotend E4
#### <a id = "PRELOAD_FILAMENT">Etapas para carregar filamentos no hotend E4:</a>
##### (https://www.youtube.com/watch?v=FyHrAMytlT8)
Se você entende o princípio de funcionamento do hotend E4, já deve saber que ao imprimir multicolorido, a máquina primeiro precisa descarregar o filamento previamente carregado do hotend e depois carregar o próximo filamento. Porém, normalmente ***a máquina não tem a capacidade de reconhecer a distância entre a extremidade frontal do filamento e o bocal antes de iniciar a impressão***. Portanto, precisamos montar um processo chamado <u>***"pre-load filaments"***</u>, que visa permitir que a máquina mova os fios finos para uma posição adequada conhecida pela máquina antes imprimindo o objeto.
:warning: ***Apenas os filamentos da extrusora que precisam ser usados no arquivo gcode precisam ser carregados no hotend E4.***

### Passos para descarregar o filamento do hotend E4:
1. Aquecimento do bico (200°C para PLA / 230°C para PETG/ABS). ***Menu: Preparar>>Filamento>>Pré-aquecer: 200/230***
2. Alimente o filamento pelo menos 10 mm na extrusora usada. ***Menu: Preparar>>Filamento>>Extrusora: 1/2/3/4; Preparar>>Filamento>>Carregar Lentamente***
3. Descarregue o filamento do hotend. ***Menu: Preparar>>Filamento>>Descarregar lentamente***

-----
## <a id = "A4">Qual é a diferença nas configurações de fatiamento entre o hotend M4 e E4:</a>
:pushpin: Essas configurações foram definidas nos perfis do software PrusaSlicer que fornecemos. Você só precisa escolher a **predefinição de impressora** correta de acordo com sua máquina e tipo de hotend.
### Configurações de fatia para impressão multicolorida
Para impressão multicolorida, as configurações de fatiamento para o hotend E4 e o hotend M4 diferem principalmente da seguinte forma:
- **iniciar gcode**
   - **Para o hotend E4**, requer "filamentos de pré-carregamento" antes de iniciar a impressão([**Saiba por que**](#PRELOAD_FILAMENT)), para obter detalhes, consulte [**start gcode do E4 hotend**][E4_STARTGCODE].
   - **Para o hotend M4**, ao imprimir no máximo 4 cores, não há necessidade de fazer alterações especiais no gcode inicial. Mas **se você precisar imprimir mais de 4 cores** (misturando filamentos de cores diferentes em várias cores), você pode definir a proporção de mistura de cores no gcode inicial. Para obter detalhes, consulte [**Como imprimir mais de 4 cores usando hot end M4**][M4_MIXMULTICOLORPRINT].
- **Configurações de retração das Extrusoras**
   - **Para o hotend E4**, o **comprimento de retração** recomendado é de 6 ~ 8 mm (deve ser inferior a 10 mm).
   - **Para o hotend M4**, o **comprimento de retração** recomendado é de 8 ~ 15 mm.
- **Torre Wipe (Torre Principal)**
:pushpin: O software de fatiamento que suporta múltiplas impressoras extrusoras tem uma opção **"Wipe Tower (Prime Tower)"**. Porque quando a impressora muda de uma extrusora para outra, muitas vezes é necessário primeiro limpar os fios finos da cor anterior no hot end. Depois de ativar a opção de apagar torre, o software de fatiamento pode gerar uma impressão “adicional” no arquivo gcode para limpar quaisquer filamentos restantes no hot end.
   - **Para o hotend E4**, o volume necessário da torre de arame é relativamente pequeno.
   - **Para o hotend M4**, o volume necessário da torre de arame é relativamente grande.
- **Código G de mudança de ferramenta**
   - **Para o hotend E4**, ao trocar a extrusora, é necessário retirar o filamento de cor anterior do hotend e depois carregar o próximo filamento de cor no hotend. Portanto, o Gcode de mudança de ferramenta precisa ser definido para realizar esta operação. Para deltails, consulte [**Código G de troca de ferramenta para hotend E4**][E4_TOOLCHANGE].
   - **Para o hotend M4**, não é necessário **Código G de troca de ferramenta**.

-----
## <a id="A5"> Como alternar entre hotend M4 e hotend E4</a>
### 1. Afrouxe os três parafusos da carcaça do hotend e remova o hotend antigo da máquina (x polia). Em seguida instale o novo hotend na máquina (x polia) e fixe os parafusos.

### 2. Conecte os fios do novo hotend à máquina.
 
### 3. Defina o tipo de hotend no menu LCD: *Control>>Configure>>Hotend Type*

#### :pushpin: Os conectores da cabeça de impressão Z9V5 estão escondidos dentro da máquina, você precisa remover o anel de borracha e retirar os conectores.

### :warning: NOTA 1: Se você não conseguir encontrar o menu "tipo hotend" na tela LCD, carregue o firmware mais recente para sua impressora.
[**:point_right: Firmware para Z9V5**][FW_Z9V5] / [**:point_right: Firmware para Z8P**][FW_Z8P] / [**:point_right: Firmware para Z9M4**][FW_Z9M4]
### :warning: NOTA 2: O hotend de cores misturadas e o hotend de cores não misturadas devem usar configurações de fatia diferentes, preste atenção para distinguir. Usar a configuração de fatia errada pode bloquear o hotend.

-----

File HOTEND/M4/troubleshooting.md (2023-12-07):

## Tourbleshooting for M4 (4-IN-1-OUT Mixing Color) Hotend
### :warning: These issue has been completely solved in M4V6, if your hotend is M4V6, you can ignore this guide.
### 1. Clogged issue
#### :question: Reasons
1. The length of the extrusion channel is longer than that of the single color.   
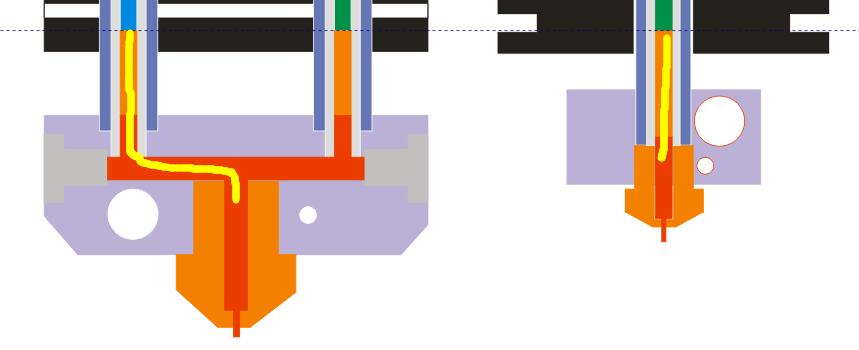
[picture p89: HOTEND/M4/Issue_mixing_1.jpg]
       
2. Since the channels at the hot end of the color mixing are interconnected, the filaments in the feed channels are also under the action of the reverse extrusion force of the other channels at the same time.  
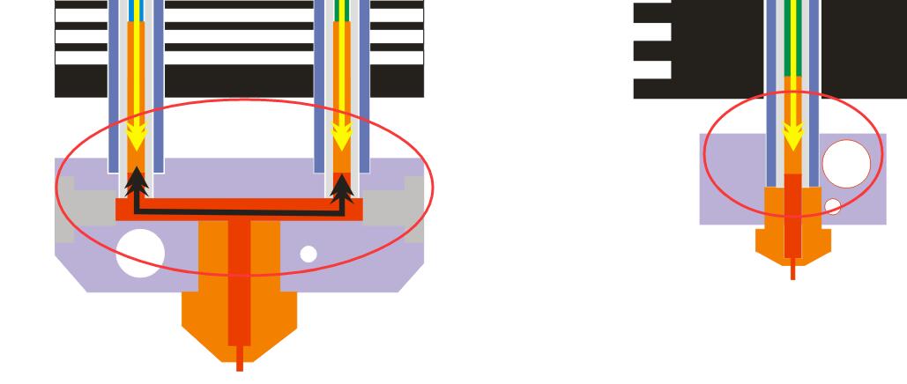
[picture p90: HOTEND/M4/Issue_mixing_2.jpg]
    
3. The longer of the filament between Tg(Glass Transition Temperature) and Tm(Melting Temperature), the greater its adhesion to the feed tube (refer to [***Hot End Design Theory***](https://reprap.org/wiki/Hot_End_Design_Theory)), and the final result will be that the extrusion feeder can't push the filament.  
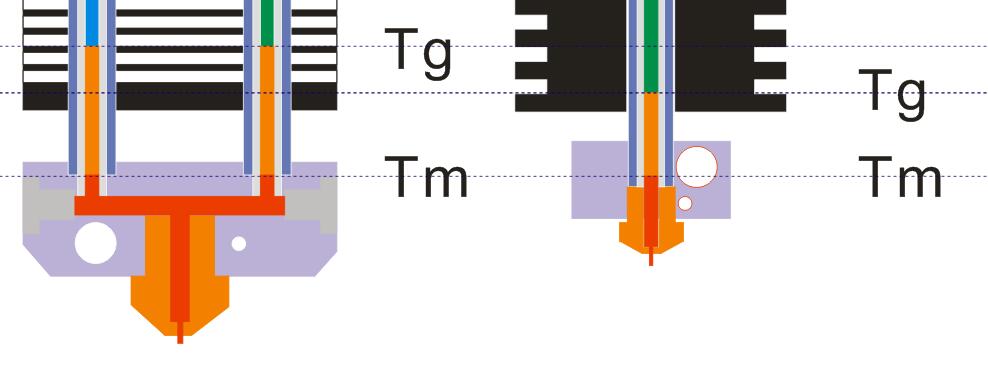
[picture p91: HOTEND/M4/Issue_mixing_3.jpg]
   
4. Other reasons: Due to weight, processing and installation restrictions, the distance between the extruder feeder and the hot end needs to be longer, it also increases the resistance of the extruder.  
#### :pill: Solutions 
1. Increase extruder force, for exmple upgrade to [**Dual gear extruder**](https://www.aliexpress.com/item/1005003473360998.html) or [**Titan extruder**](https://www.aliexpress.com/item/1005001678239017.html) .  
2. Choose harder filaments, for example **PLA+** > **PLA** > **silk-PLA**.  
3. Reduce the heat transfer rate of **Insulation block** and keep the "Heat sink" cool, to short the filament distance between Tg and Tm.  
4. Minimize the length of the mixing chamber channels.   
5. Improve retraction settings.  
6. Do not leave the channel unused for a long time, filament in Tg state for a long time will be more firmly attached to the filament guide.
 
### 2. Strings issue
#### :question: Reasons
Because there is a mixing color chamber, so the stored filaments in the mixing color hotend is bigger than single color hotend, it will reduce the effect of retraction.  
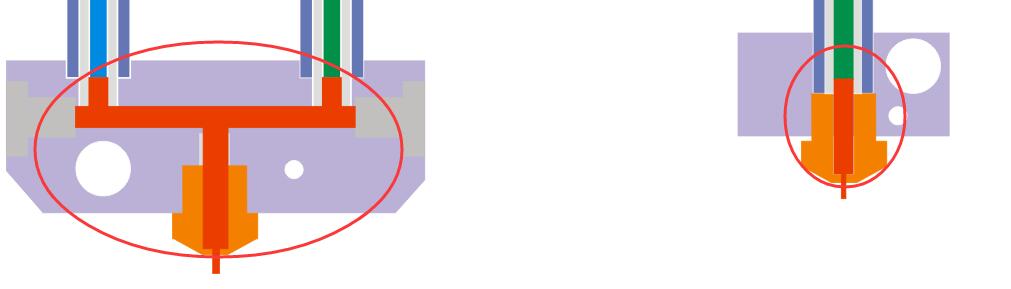
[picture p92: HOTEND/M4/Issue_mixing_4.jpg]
   
#### :pill: Solutions  
##### 1. Reduce the size of mixing color chamber, for example, upgrade to [**small store room nozzle**](https://www.aliexpress.com/item/1005001447928770.html).  
##### 2. Add "wipe" on silcing settings.
###### Cura Slicer (Coasting)
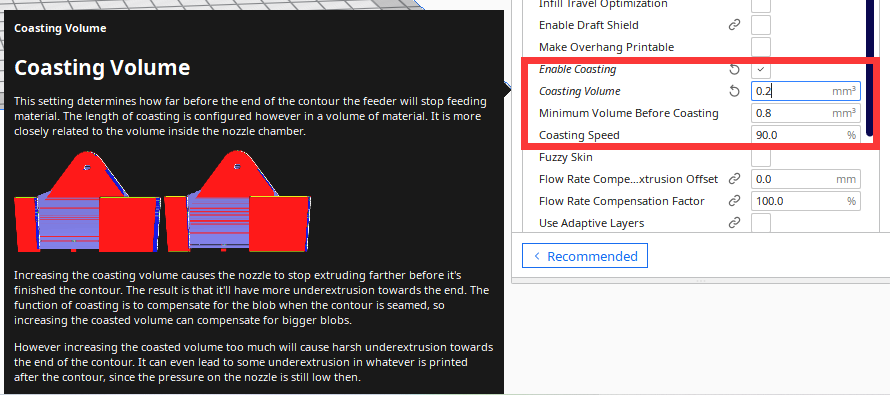
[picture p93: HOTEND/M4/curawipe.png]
Cura

###### PrusaSlicer (Wipe while retracting)
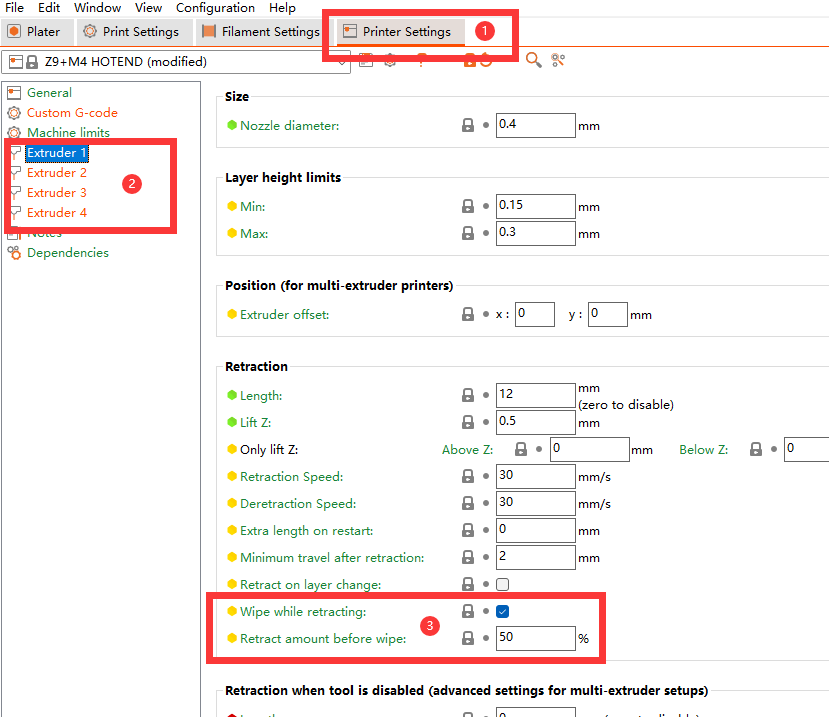
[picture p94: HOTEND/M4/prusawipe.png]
PrusaSlicer

##### 3. Turn on auto synchronous retraction feature. For detail, please refer to [**here**](https://github.com/ZONESTAR3D/Upgrade-kit-guide/tree/main/HOTEND/M4%20%204-IN-1-OUT%20Mixing%20Color%20Hotend/Example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)
##### 4. If you are very concerned about strings issue, it is recommended that you buy a single color or 4-IN-1-OUT Non-mix color Hotend.
- :book: [**4-IN-1-OUT Non-Mix Color Hotend**](../E4%204-IN-1-OUT%20Non-Mixing%20Color%20Hotend/example/readme.md)
- :gift: [**4-IN-1-OUT Non-Mix Color Hotend**](https://www.aliexpress.com/item/1005002951777699.html)

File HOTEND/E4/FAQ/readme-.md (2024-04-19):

[E4FAQ1]:https://github.com/ZONESTAR3D/Upgrade-kit-guide/blob/main/HOTEND/E4/User_guide/readme.md#5-working-principle
[E4FAQ2]:https://github.com/ZONESTAR3D/Slicing-Guide/blob/master/PrusaSlicer/Custom_Gcode.md
[E4FAQ3]:https://github.com/ZONESTAR3D/Slicing-Guide/blob/master/PrusaSlicer/PrusaSlicerGuide_E4.md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
[E4FAQ4]:https://github.com/ZONESTAR3D/Slicing-Guide/blob/master/PrusaSlicer/Custom_Gcode.md#tool-change-g-code
[E4FAQ5]:https://github.com/ZONESTAR3D/Slicing-Guide/blob/master/cura/E4_hotend/readme.md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
[E4FAQ6]:https://github.com/ZONESTAR3D/Upgrade-kit-guide/blob/main/HOTEND/E4/User_guide/readme.md#2-components
[BMG]: https://github.com/ZONESTAR3D/Upgrade-kit-guide/tree/main/Dual_Gear_Extruder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

----
## <a id="choose-language">:globe_with_meridians: Choose language </a>











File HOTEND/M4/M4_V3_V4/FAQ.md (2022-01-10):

## FAQ for mixing color hotend
### :question: Hotend is clogged/blocked 
If you encounter the problem of hot end clogged / blocked, please check according to the following items:  
#### Check Slicing settings.   
:red_circle: **Disable “Extruder/Nozzle switching retraction”.**
For example, set “Nozzle Switch Retraction Distance” to 0 in Cura.   
:red_circle: **Set the print speed low than 50mm/s.**  
#### Check filament    
:red_circle: **Don't mix different type of filament.**   
:bulb: Mixing ABS and PLA / PLA + is usually no problem, but PETG or silk PLA, wood-pla, transparent PLA and other materials mixed with many additives are usually easy to cause blockage.  
:bulb: When loading the filament to the hotend, please make sure that the filament enter the heating block of the hot end, it is about 45mm deep into the hot end.
#### Check nozzle
:red_circle: There may be impurities in the filament that cannot melt, resulting in nozzle blockage.   
:key: Refer to the "How to clean the cloged mixing color hotend" to clean the hotend and replace a new nozzle.  
:red_circle: When printing, the first layer is too close, resulting in the nozzle scraping on the glass, or the front end of the nozzle may be damaged and blocked.  
:key: Refer to the "How to clean the cloged mixing color hotend" to replace a new nozzle.   
#### Check distance from nozzle to bed  
:red_circle:If the distance from nozzle to bed is too closed, it will cause the filament can't flow out from the nozzle.   
:key: Double click the knob to fine tune the distance from the nozzle to the Printing platform.   
:bulb: When slicing, use the "shaft" base, and set the distance of the first layer to more than 0.5mm as far as possible, which can effectively reduce the trouble of adjusting the z-axis distance each time.  
#### Check temperature of hot end 
:red_circle: Hot end cooling fan must work when the nozzle temperature is over 50 degree, otherwise it will cause clogged because the inner PTFE tube overheat.  
#### Check extruder motor 
:key: Check whether the extruder is installed properly.    
  
:key: Properly adjust the extruder pressure.


### :question: Filament leaked from the hotend
:white_medium_small_square: TODO: wait to add.
 
### :question: There are mottled colors (when printing multi-color)
:white_medium_small_square: TODO: wait to add.

### How to clean the cloged mixing color hotend
+ **Step 1:** Heat the hot end (nozzle) to 200 degrees and wait for the temperature to be reached
+ **Step 2:** Remove the fitting and pull out the filament (Figure 1).  
:sunny: **Tips1:** If it is difficult to pull out the filaments, you can use the cutting pliers to clamp the filaments and pull out (Figure 2).  
:sunny:**Tips2:** If the filaments cannot be pulled out at all, you can use cutting pliers to cut the filaments.  
+ **Step 3:** Remove the nozzle from the hot end.  
:memo: **Note:** Please pay attention to prevent burns, it is recommended to wear heat-resistant gloves for operation.  
+ **Step 4:** Install the hotend-clean-tool on the hot-end (Figure 3), close the channels that are not blocked, and leave only the blocked
channel.  
:sunny: **Tips:** If the hot end is blocked by filaments and cannot be inserted into the hotend-clean-tool, you can use a lighter to heat the thin rod of the hotend-clean-tool, and then insert it to the hotend(Figure 4).  
+ **Step 5:** Manually feed in at least 50cm filaments slowly from the hotend (Figure 5).  
+ **Step 6:** Clean the filaments in front of the hotend (Figure 6). If necessary (there are other channels are blocked), you can close the cleaned channel with a “hotend cleaning tool” before cleaning the next channel.  
+ **Step 7:** Install the nozzle back.  
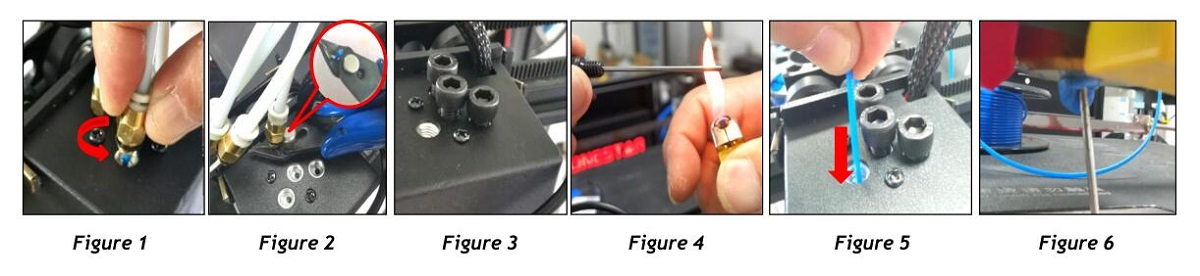
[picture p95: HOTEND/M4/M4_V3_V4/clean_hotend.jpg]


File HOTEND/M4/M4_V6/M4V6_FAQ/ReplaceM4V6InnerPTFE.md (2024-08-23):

## <a id="choose-language">:globe_with_meridians: Choose language </a>











----
## <a id="en">How to replace the inner PTFE tubes of the M4V6 hotend</a>
### Steps
1. Prepare 4 piece PTFE tube (ID=2mm / OD=4mm), length is about 100mm (***Fig1***). To cut the PTFE pipe by a knife (paper cutter) and try to keep the front end flat.
2. Remove the screws which to fix the hot end on the top of the hot end housing (***Fig2***).
3. Loosen the screws which to fix the heater and temperature sensor (***Fig3***).
4. Remove the heater and temperature sensor from the hot end (***Fig4***).
5. Remove the hot end from the housing (***Fig5***).
6. Remove the 2 screws to fix the heating block (***Fig6***).
7. Pull out the heating block (***Fig7***).
8. Press the “RED ring” of the fittings and pull out the PTFE tubes (***Fig8***).
9. Insert the new PTFE tubes and install the heating block back in reverse order.
10. Push the PTFE tubes to the bottom after installed the heating block.
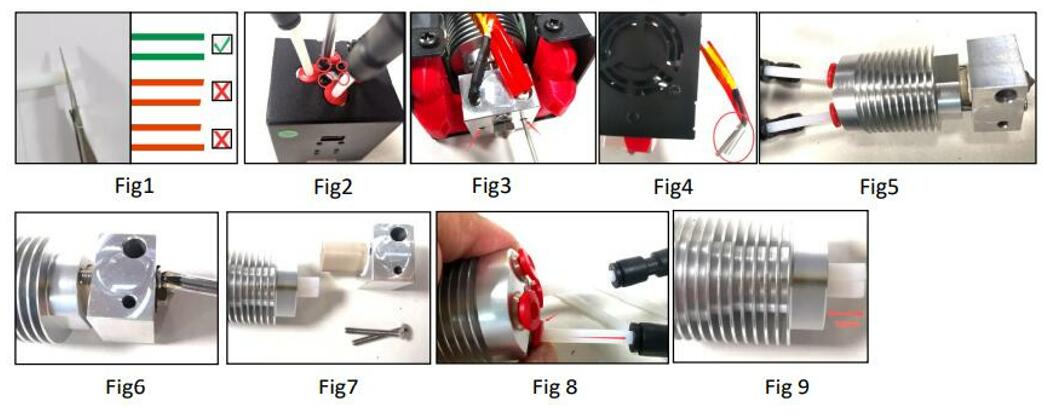
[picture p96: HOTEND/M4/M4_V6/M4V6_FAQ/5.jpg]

### Video tutorial
(https://www.youtube.com/watch?v=S-vUdI5z-nM)

----
## <a id="es">Cómo reemplazar los tubos de PTFE internos del hotend M4V6</a>
### Pasos
1. Prepare 4 piezas de tubo de PTFE (DI=2 mm / DE=4 mm), la longitud es de aproximadamente 100 mm (***Fig1***). Corte el tubo de PTFE con un cuchillo (cortador de papel) e intente mantener el extremo frontal plano.
2. Retire los tornillos que fijan el hotend en la parte superior de la carcasa del hotend (***Fig2***).
3. Afloje los tornillos que fijan el calentador y el sensor de temperatura (***Fig3***).
4. Retire el calentador y el sensor de temperatura del hotend (***Fig4***).
5. Retire el hotend de la carcasa (***Fig5***).
6. Retire los 2 tornillos para fijar el bloque de calentamiento (***Fig6***).
7. Extraiga el bloque de calentamiento (***Fig7***).
8. Presione el “anillo ROJO” de los accesorios y extraiga los tubos de PTFE (***Fig. 8***).
9. Inserte los nuevos tubos de PTFE e instale el bloque calefactor nuevamente en orden inverso.
10. Empuje los tubos de PTFE hasta el fondo después de instalar el bloque calefactor.

### Video tutorial
(https://www.youtube.com/watch?v=S-vUdI5z-nM)

----
## <a id="pt">Como substituir os tubos internos de PTFE do hotend M4V6</a>
### Passos
1.º Prepare um tubo de PTFE de 4 peças (ID=2mm / OD=4mm), o comprimento é de cerca de 100mm (***Fig1***). Corte o tubo de PTFE com uma faca (cortador de papel) e tente manter a extremidade frontal plana.
2.º Retire os parafusos que fixam o hot end na parte superior do alojamento do hot end (***Fig2***).
3.º Desaperte os parafusos que fixam o aquecedor e o sensor de temperatura (***Fig3***).
4.º Retire o aquecedor e o sensor de temperatura da extremidade quente (***Fig4***).
5.º Retire a extremidade quente da caixa (***Fig5***).
6.º Retire os 2 parafusos de fixação do bloco de aquecimento (***Fig6***).
7.º Retire o bloco de aquecimento (***Fig7***).
8.º Pressione o “anel VERMELHO” das ligações e retire os tubos de PTFE (***Fig8***).
9.º Insira os novos tubos de PTFE e volte a instalar o bloco de aquecimento pela ordem inversa.
10.º Empurre os tubos de PTFE para o fundo depois de instalar o bloco de aquecimento.

### Tutorial em vídeo
(https://www.youtube.com/watch?v=S-vUdI5z-nM)

----
## <a id="fr">Comment remplacer les tubes intérieurs en PTFE de la tête chauffante M4V6</a>
### Étapes
1. Préparez un tube en PTFE de 4 pièces (ID = 2 mm / OD = 4 mm), la longueur est d'environ 100 mm (***Fig1***). Coupez le tube en PTFE avec un couteau (coupe-papier) et essayez de garder l'extrémité avant plate.
2. Retirez les vis qui fixent la tête chauffante sur le dessus du boîtier de la tête chauffante (***Fig2***).
3. Desserrez les vis qui fixent le chauffage et le capteur de température (***Fig3***).
4. Retirez le chauffage et le capteur de température de la tête chauffante (***Fig4***).
5. Retirez la tête chauffante du boîtier (***Fig5***).
6. Retirez les 2 vis pour fixer le bloc chauffant (***Fig6***).
7. Retirez le bloc chauffant (***Fig7***).
8. Appuyez sur la « bague ROUGE » des raccords et retirez les tubes PTFE (***Fig8***).
9. Insérez les nouveaux tubes PTFE et réinstallez le bloc chauffant dans l'ordre inverse.
10. Poussez les tubes PTFE vers le bas après avoir installé le bloc chauffant.

### Tutoriel vidéo
(https://www.youtube.com/watch?v=S-vUdI5z-nM)

----
## <a id="de">So ersetzen Sie die inneren PTFE-Schläuche des M4V6-Hotends</a>
### Schritte
1. Bereiten Sie 4 PTFE-Schläuche (Innendurchmesser = 2 mm / Außendurchmesser = 4 mm) vor, die Länge beträgt etwa 100 mm (***Abb. 1***). Schneiden Sie das PTFE-Rohr mit einem Messer (Papierschneider) ab und versuchen Sie, das vordere Ende flach zu halten.
2. Entfernen Sie die Schrauben, mit denen das Hotend oben am Hotend-Gehäuse befestigt ist (***Abb. 2***).
3. Lösen Sie die Schrauben, mit denen die Heizung und der Temperatursensor befestigt sind (***Abb. 3***).
4. Entfernen Sie die Heizung und den Temperatursensor vom Hotend (***Abb. 4***).
5. Entfernen Sie das Hotend vom Gehäuse (***Abb. 5***).
6. Entfernen Sie die 2 Schrauben, mit denen der Heizblock befestigt ist (***Abb. 6***).
7. Ziehen Sie den Heizblock heraus (***Abb. 7***).
8. Drücken Sie auf den „ROTEN Ring“ der Anschlüsse und ziehen Sie die PTFE-Schläuche heraus (***Abb. 8***). 9. Setzen Sie die neuen PTFE-Schläuche ein und installieren Sie den Heizblock in umgekehrter Reihenfolge wieder.
10. Schieben Sie die PTFE-Schläuche nach der Installation des Heizblocks nach unten.

### Video-Tutorial
(https://www.youtube.com/watch?v=S-vUdI5z-nM)

----
## <a id="it">Come sostituire i tubi interni in PTFE dell'hotend M4V6</a>
### Passaggi
1. Preparare 4 pezzi di tubo in PTFE (ID=2mm / OD=4mm), lunghezza circa 100mm (***Fig1***). Tagliare il tubo in PTFE con un coltello (taglierino) e cercare di mantenere la parte anteriore piatta.
2. Rimuovere le viti che fissano l'hot end sulla parte superiore dell'alloggiamento dell'hot end (***Fig2***).
3. Allentare le viti che fissano il riscaldatore e il sensore di temperatura (***Fig3***).
4. Rimuovere il riscaldatore e il sensore di temperatura dall'hot end (***Fig4***).
5. Rimuovere l'hot end dall'alloggiamento (***Fig5***).
6. Rimuovere le 2 viti per fissare il blocco riscaldante (***Fig6***).
7. Estrarre il blocco riscaldante (***Fig7***).
8. Premere l'"anello ROSSO" dei raccordi ed estrarre i tubi in PTFE (***Fig8***).
9. Inserire i nuovi tubi in PTFE e reinstallare il blocco riscaldante in ordine inverso.
10. Spingere i tubi in PTFE verso il basso dopo aver installato il blocco riscaldante.

### Video tutorial
(https://www.youtube.com/watch?v=S-vUdI5z-nM)

----
## <a id="ru">Как заменить внутренние трубки ПТФЭ горячего конца M4V6</a>
### Шаги
1. Подготовьте 4 трубки ПТФЭ (внутренний диаметр = 2 мм / внешний диаметр = 4 мм), длина около 100 мм (***Рис.1***). Отрежьте трубку ПТФЭ ножом (резаком для бумаги) и постарайтесь сохранить передний конец плоским.
2. Открутите винты, которые крепят горячий конец на верхней части корпуса горячего конца (***Рис.2***).
3. Ослабьте винты, которые крепят нагреватель и датчик температуры (***Рис.3***).
4. Снимите нагреватель и датчик температуры с горячего конца (***Рис.4***).
5. Снимите горячий конец с корпуса (***Рис.5***).
6. Открутите 2 винта, чтобы закрепить нагревательный блок (***Рис.6***).
7. Вытащите нагревательный блок (***Рис.7***).
8. Нажмите на «КРАСНОЕ кольцо» фитингов и вытащите трубки ПТФЭ (***Рис.8***).
9. Вставьте новые трубки ПТФЭ и установите нагревательный блок в обратном порядке.
10. Протолкните трубки ПТФЭ вниз после установки нагревательного блока.

### Видеоруководство
(https://www.youtube.com/watch?v=S-vUdI5z-nM)

----
## <a id="jp">M4V6 ホットエンドの内部 PTFE チューブの交換方法</a>
### 手順
1. 長さ約 100mm の PTFE チューブ (ID=2mm / OD=4mm) を 4 本用意します (***図 1***)。PTFE パイプをナイフ (ペーパー カッター) で切断し、先端が平らになるようにします。
2. ホットエンドをホットエンド ハウジングの上部に固定しているネジを取り外します (***図 2***)。
3. ヒーターと温度センサーを固定しているネジを緩めます (***図 3***)。
4. ヒーターと温度センサーをホットエンドから取り外します (***図 4***)。
5. ホットエンドをハウジングから取り外します (***図 5***)。
6. 加熱ブロックを固定している 2 本のネジを取り外します (***図 6***)。
7. 加熱ブロックを引き出します (***図 7***)。
8. フィッティングの「赤いリング」を押して、PTFE チューブを引き出します (***図 8***)。
9. 新しい PTFE チューブを挿入し、逆の順序で加熱ブロックを取り付けます。
10. 加熱ブロックを取り付けた後、PTFE チューブを一番下まで押し込みます。

### ビデオ チュートリアル
(https://www.youtube.com/watch?v=S-vUdI5z-nM)

----
## <a id="kr">M4V6 핫엔드의 내부 PTFE 튜브를 교체하는 방법</a>
### 단계
1. 4개의 PTFE 튜브(ID=2mm / OD=4mm)를 준비합니다. 길이는 약 100mm입니다(***그림1***). 칼(종이 커터)로 PTFE 파이프를 자르고 전면을 평평하게 유지하려고 합니다.
2. 핫엔드를 핫엔드 하우징 상단에 고정하는 나사를 제거합니다(***그림2***).
3. 히터와 온도 센서를 고정하는 나사를 풉니다(***그림3***).
4. 핫엔드에서 히터와 온도 센서를 제거합니다(***그림4***).
5. 하우징에서 핫엔드를 제거합니다(***그림5***).
6. 가열 블록을 고정하는 나사 2개를 제거합니다(***그림6***).
7. 가열 블록을 꺼냅니다(***그림7***).
8. 피팅의 "RED 링"을 누르고 PTFE 튜브를 빼냅니다(***그림8***).
9. 새로운 PTFE 튜브를 삽입하고 가열 블록을 역순으로 다시 설치합니다.
10. 가열 블록을 설치한 후 PTFE 튜브를 바닥으로 밀어 넣습니다.

### 비디오 튜토리얼
(https://www.youtube.com/watch?v=S-vUdI5z-nM)

----
## <a id="ar">كيفية استبدال أنابيب PTFE الداخلية للطرف الساخن M4V6</a>
### الخطوات
1. قم بإعداد أنبوب PTFE مكون من 4 قطع (القطر الداخلي = 2 مم / القطر الخارجي = 4 مم)، ويبلغ طوله حوالي 100 مم (***الشكل 1***). قم بقطع أنبوب PTFE بسكين (قاطع ورق) وحاول الحفاظ على الطرف الأمامي مسطحًا.
2. قم بإزالة البراغي التي تستخدم لتثبيت الطرف الساخن في الجزء العلوي من غلاف الطرف الساخن (***الشكل 2***).
3. قم بفك البراغي التي تستخدم لتثبيت السخان ومستشعر درجة الحرارة (***الشكل 3***).
4. قم بإزالة السخان ومستشعر درجة الحرارة من الطرف الساخن (***الشكل 4***).
5. قم بإزالة الطرف الساخن من الغلاف (***الشكل 5***).
6. قم بإزالة البراغيين لتثبيت كتلة التسخين (***الشكل 6***).
7. اسحب كتلة التسخين (***الشكل 7***).
8. اضغط على "الحلقة الحمراء" للتجهيزات واسحب أنابيب PTFE للخارج (***الشكل 8***).
9. أدخل أنابيب PTFE الجديدة وقم بتثبيت كتلة التسخين مرة أخرى بترتيب عكسي.
10. ادفع أنابيب PTFE إلى الأسفل بعد تثبيت كتلة التسخين.

### فيديو تعليمي
(https://www.youtube.com/watch?v=S-vUdI5z-nM)

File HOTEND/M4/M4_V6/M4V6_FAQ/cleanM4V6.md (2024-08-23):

[loadfilament]: https://github.com/ZONESTAR3D/Z8P/blob/main/Z8P-MK2/2-Operation_Guide/readme.md#load-filaments

----
## <a id="choose-language">:globe_with_meridians: Choose language </a>











----
## <a id="en">How to clean the clogged M4V6 hot end</a>
- **Step 1: Heating the nozzle to 260 degree.**       
  *Prepare>>Filament>>Preheat nozzle: 260*, wait the nozzle reached 260 degree.
- **Step 2: Load all 4 filaments to the hot end.**    
- **Step 3: Extruder 4 filaments simultaneously, until you can see the filament is flowed out from the nozzle.**     
    *Prepare>>Filament>>extruder: all*      
    *Prepare>>Filament>>slowly load*, you may need to do a few times, until all 4 filaments have flowed out from the nozzle.
- **Step 4: Extrude 4 filaments one by one**     
    *Prepare>>Filament>>extruder: 1*     
    *Prepare>>Filament>>extruder: slowly load*, until you see the filament of extruder #1 is flowing out from the nozzle.     
    *Prepare>>Filament>>extruder: 2*    
    *Prepare>>Filament>>extruder: slowly load*, until you see the filament of extruder #2 is flowing out from the nozzle.    
    *Prepare>>Filament>>extruder: 3*    
    *Prepare>>Filament>>extruder: slowly load*, until you see the filament of extruder #3 is flowing out from the nozzle.    
    *Prepare>>Filament>>extruder: 4*     
    *Prepare>>Filament>>extruder: slowly load*, until you see the filament of extruder #3 is flowing out from the nozzle.     
#### 
[Video tutorial](https://github.com/ZONESTAR3D/Z8P/assets/29502731/72312727-5ce5-4a35-8f2a-49f9145557ac)
#### :pushpin: If the hot end cannot be cleaned by doing the above steps, or the hot end is still easily clogged after cleaning, please do remove the nozzle and do once above steps to clean the hotend again, and then install a new nozzle. About how to replace a nozzle, please watch this **[:clapper: video tutorial](https://youtu.be/L5VRyEbsJvM).**
#### :pushpin: If the filaments cannot be inserted into the "inner PTFE tubes" at the M4V6 hot end, please refer to this guide ([:book: How to replace the inner PTFE tubes](./ReplaceM4V6InnerPTFE.md)) to replace the blocked inner PTFE tubes.

### Why is the hotend clogged?
There are some reasons that may cause the hotend to be blocked, please check the list one by one to ensure that you have noticed these matters.
#### Incorrect steps/methods for loading filament
:pushpin: When loading the filament to the hotend, please ensure that the filaments enter the bottom of the hot end.    
:pushpin: You need to load all the 4 filaments to the hot end whether printing one or multi color 3d prints.    
For how to load filaments, please refer to [:book: this guide](#loadfilament) or the [:clapper: video tutorial](https://youtu.be/-47yB95uIxI).
#### Nozzle is defective
The nozzle may also be partially clogged. If you find the filament flowed out from the nozzle is thinner than normal, the nozzle may be partially clogged, please replace a new nozzle directly.  
#### The nozzle is too close to the print platform
If the nozzle is too close to the hot bed when printing the first layer, the filament may not be ejected. If this is maintained for a long time, it may cause the filament in the hot end to be over-compressed and cause blockage (often blocked at the entrance of hotend). When printing the first layer, pay attention to the distance between the nozzle and the hot bed. If necessary, open the "BabyStep" menu to adjust the nozzle height.
#### Incorrect "switch retraction distance" setting in the slice settings
For 4-IN-1-OUT mix color hotend, the **"Extruder switching retraction length"** MUST be set to 0. For example, set **“Nozzle Switch Retraction Distance”** to 0 in Cura Slicer and set **"Retraction when tool is disable"** in PrusaSlicer.  
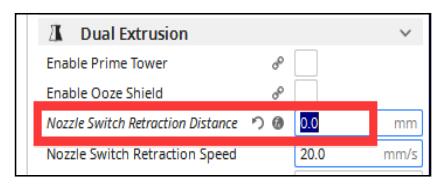
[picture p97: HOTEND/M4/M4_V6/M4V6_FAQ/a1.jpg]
 

### :envelope: If you can't find a solution to solve your problem after readed the FAQ , please contact our technical support team by [:e-mail:](support@zonestar3d.com) .

----
## <a id="es">Cómo limpiar el hot end M4V6 obstruido</a>  [:arrow_heading_up:](#choose-language)
- **Paso 1: Calienta la boquilla a 260 grados.**
*Preparar>>Filamento>>Precalentar la boquilla: 260*, esperar a que la boquilla alcance los 260 grados.
- **Paso 2: Carga los 4 filamentos en el hot end.**
- **Paso 3: Extruye los 4 filamentos simultáneamente, hasta que puedas ver que el filamento sale por la boquilla.**
*Preparar>>Filamento>>extrusor: todo*
*Preparar>>Filamento>>cargar lentamente*, es posible que tengas que hacerlo varias veces, hasta que los 4 filamentos hayan salido por la boquilla.
- **Paso 4: Extruye 4 filamentos uno por uno**    
*Preparar >> Filamento >> extrusor: 1*    
*Preparar >> Filamento >> extrusor: carga lentamente*, hasta que veas que el filamento del extrusor n.° 1 sale por la boquilla.    
*Preparar >> Filamento >> extrusor: 2*    
*Preparar >> Filamento >> extrusor: carga lentamente*, hasta que veas que el filamento del extrusor n.° 2 sale por la boquilla.    
*Preparar >> Filamento >> extrusor: 3*    
*Preparar >> Filamento >> extrusor: carga lentamente*, hasta que veas que el filamento del extrusor n.° 3 sale por la boquilla.    
*Preparar >> Filamento >> Extrusor: 4*    
*Preparar >> Filamento >> Extrusor: cargar lentamente*, hasta que vea que el filamento del extrusor n.° 3 sale por la boquilla.    
####
[Tutorial en video](https://github.com/ZONESTAR3D/Z8P/assets/29502731/72312727-5ce5-4a35-8f2a-49f9145557ac)
#### :pushpin: Si no se puede limpiar el extremo caliente siguiendo los pasos anteriores, o si el extremo caliente sigue obstruyéndose fácilmente después de la limpieza, retire la boquilla y vuelva a realizar los pasos anteriores para limpiar el extremo caliente y, luego, instale una boquilla nueva. Para saber cómo reemplazar una boquilla, mira este **[:clapper: video tutorial](https://youtu.be/L5VRyEbsJvM).**
#### :pushpin: Si los filamentos no se pueden insertar en los "tubos de PTFE internos" en el hotend M4V6, consulta esta guía ([:book: Cómo reemplazar los tubos de PTFE internos](./ReplaceM4V6InnerPTFE.md)) para reemplazar los tubos de PTFE internos bloqueados.

### ¿Por qué está obstruido el hotend?
Hay algunas razones que pueden hacer que el hotend se bloquee, revisa la lista una por una para asegurarte de haber notado estos problemas.
#### Pasos/métodos incorrectos para cargar filamento
:pushpin: Al cargar el filamento en el hotend, asegúrate de que los filamentos ingresen por la parte inferior del hotend.
:pushpin: Debes cargar los 4 filamentos en el hot end, ya sea que imprimas impresiones 3D de un solo color o de varios colores.
Para saber cómo cargar filamentos, consulta [:book: esta guía](#loadfilament) o el [:clapper: video tutorial](https://youtu.be/-47yB95uIxI).
#### La boquilla está defectuosa
La boquilla también puede estar parcialmente obstruida. Si ves que el filamento que sale de la boquilla es más fino de lo normal, es posible que la boquilla esté parcialmente obstruida. Reemplaza la boquilla directamente por una nueva.
#### La boquilla está demasiado cerca de la plataforma de impresión
Si la boquilla está demasiado cerca de la cama caliente al imprimir la primera capa, es posible que no se expulse el filamento. Si esto se mantiene durante mucho tiempo, puede provocar que el filamento en el hot end se comprima demasiado y provoque un bloqueo (a menudo, se bloquea en la entrada del hot end). Al imprimir la primera capa, presta atención a la distancia entre la boquilla y la cama caliente. Si es necesario, abra el menú "BabyStep" para ajustar la altura de la boquilla.
#### Configuración incorrecta de la "distancia de retracción del interruptor" en la configuración de corte
Para el hotend de mezcla de colores 4-IN-1-OUT, la **"Longitud de retracción del interruptor del extrusor"** DEBE estar configurada en 0. Por ejemplo, configure **“Distancia de retracción del interruptor de la boquilla”** en 0 en Cura Slicer y configure **“Retracción cuando la herramienta está deshabilitada”** en PrusaSlicer.
 

### :envelope: Si no puede encontrar una solución para resolver su problema después de leer las preguntas frecuentes, comuníquese con nuestro equipo de soporte técnico por [:e-mail:](support@zonestar3d.com) .

----
## <a id="pt">Como limpar o hot end M4V6 entupido</a> [:arrow_heading_up:](#choose-language)
- **Passo 1: Aquecer o bico a 260 graus.**
 *Prepare>>Filament>>Pré-aqueça o bico: 260*, aguarde que o bico atinja os 260 graus.
- **Passo 2: Carregue todos os 4 filamentos na extremidade quente.**
- **Passo 3: Extrusora 4 filamentos em simultâneo, até que se consiga ver que o filamento flui para fora do bico.**
 *Preparar>>Filamento>>extrusora: tudo*    
 *Preparar>>Filament>>carregar lentamente*, pode ser necessário fazê-lo algumas vezes, até que todos os 4 filamentos tenham saído do bocal.
- **Etapa 4: Extrusão de 4 filamentos um a um**    
 *Preparar>>Filamento>>extrusora: 1*    
 *Prepare>>Filamento>>extrusora: carregue lentamente*, até ver que o filamento da extrusora nº 1 está a fluir para fora do bocal.    
 *Preparar>>Filamento>>extrusora: 2*    
 *Prepare>>Filamento>>extrusora: carregue lentamente*, até ver que o filamento da extrusora nº 2 está a fluir para fora do bocal.    
 *Preparar>>Filamento>>extrusora: 3*    
 *Prepare>>Filamento>>extrusora: carregue lentamente*, até ver que o filamento da extrusora nº 3 está a fluir para fora do bocal.    
 *Preparar>>Filamento>>extrusora: 4*    
 *Prepare>>Filamento>>extrusora: carregue lentamente*, até ver que o filamento da extrusora nº 3 está a fluir para fora do bocal.    
####
[Tutorial em vídeo](https://github.com/ZONESTAR3D/Z8P/assets/29502731/72312727-5ce5-4a35-8f2a-49f9145557ac)
#### :pushpin: Se a extremidade quente não puder ser limpa seguindo os passos acima, ou se a extremidade quente ainda estiver facilmente entupida após a limpeza, retire o bocal e siga os passos acima para limpar novamente a extremidade quente e, em seguida, instale um novo bocal. Sobre como substituir um bico, veja este **[:clapper: vídeo tutorial](https://youtu.be/L5VRyEbsJvM).**
#### :pushpin: Se os filamentos não puderem ser inseridos nos "tubos internos de PTFE" na extremidade quente M4V6, consulte este guia ([:book: Como substituir os tubos internos de PTFE](./ReplaceM4V6InnerPTFE.md )) para substituir os tubos internos de PTFE bloqueados.

### Porque é que o hotend está entupido?
Existem alguns motivos que podem fazer com que o hotend seja bloqueado.
#### Passos/métodos incorretos para carregar o filamento
:pin: Ao carregar o filamento no hotend, certifique-se de que os filamentos entram na parte inferior do hotend.
:pushpin: É necessário carregar todos os 4 filamentos no hot end, seja a imprimir impressões 3D de uma ou várias cores.
Para saber como carregar filamentos, consulte [:book: este guia](#loadfilament) ou o [:clapper: vídeo tutorial](https://youtu.be/-47yB95uIxI).
#### Bocal está com defeito
O bocal também pode estar parcialmente entupido. Se achar que o filamento que sai do bico é mais fino do que o normal, o bico pode estar parcialmente entupido, substitua diretamente um novo bico.
#### O bocal está demasiado próximo da plataforma de impressão
Se o bocal estiver demasiado próximo da cama quente ao imprimir a primeira camada, o filamento poderá não ser ejetado. Se isto for mantido durante um longo período, pode fazer com que o filamento no hotend fique sobrecomprimido e cause bloqueio (geralmente bloqueado na entrada do hotend). Ao imprimir a primeira camada, tenha em atenção a distância entre o bico e a cama quente. Se necessário, abra o menu “BabyStep” para ajustar a altura do bico.
#### Configuração incorreta de "alterar distância de retração" nas definições de corte
Para o hotend de cores misturadas 4-IN-1-OUT, o **"Extrusor switching retraction length"** DEVE ser definido como 0. Por exemplo, defina **“Nozzle Switch Retraction Distance”** para 0 no Cura Slicer e defina **"Retração quando a ferramenta está desativada"** no PrusaSlicer.
 

### :envelope: Se não encontrar uma solução para resolver o seu problema após ler as FAQ, por favor contacte a nossa equipa de suporte técnico através de [:e-mail:](support@zonestar3d.com).

----
## <a id="fr">Comment nettoyer la tête chauffante M4V6 obstruée</a> [:arrow_heading_up:](#choose-language)
- **Étape 1 : Chauffer la buse à 260 degrés.**
*Préparer>>Filament>>Préchauffer la buse : 260*, attendre que la buse atteigne 260 degrés.
- **Étape 2 : Charger les 4 filaments dans la tête chauffante.**
- **Étape 3 : Extruder 4 filaments simultanément, jusqu'à ce que vous puissiez voir le filament sortir de la buse.**
*Préparer>>Filament>>extrudeuse : tous*
*Préparer>>Filament>>charger lentement*, vous devrez peut-être le faire plusieurs fois, jusqu'à ce que les 4 filaments sortent de la buse.
- **Étape 4 : extrudez 4 filaments un par un**
*Préparez>>Extrudeuse de filament : 1*    
*Préparez>>Extrudeuse de filament : chargez lentement*, jusqu'à ce que vous voyiez le filament de l'extrudeuse n°1 sortir de la buse.    
*Préparez>>Extrudeuse de filament : 2*    
*Préparez>>Extrudeuse de filament : chargez lentement*, jusqu'à ce que vous voyiez le filament de l'extrudeuse n°2 sortir de la buse.    
*Préparez>>Extrudeuse de filament : 3*    
*Préparez>>Extrudeuse de filament : chargez lentement*, jusqu'à ce que vous voyiez le filament de l'extrudeuse n°3 sortir de la buse.    
*Préparez >>Filament>>extrudeuse : 4*    
*Préparez >>Filament>>extrudeuse : chargez lentement*, jusqu'à ce que vous voyiez le filament de l'extrudeuse n° 3 sortir de la buse.    
####
[Tutoriel vidéo](https://github.com/ZONESTAR3D/Z8P/assets/29502731/72312727-5ce5-4a35-8f2a-49f9145557ac)
#### :pushpin: Si l'extrémité chaude ne peut pas être nettoyée en suivant les étapes ci-dessus, ou si l'extrémité chaude est toujours facilement obstruée après le nettoyage, veuillez retirer la buse et effectuer une fois les étapes ci-dessus pour nettoyer à nouveau l'extrémité chaude, puis installer une nouvelle buse. Pour savoir comment remplacer une buse, veuillez regarder ce **[:clapper: tutoriel vidéo](https://youtu.be/L5VRyEbsJvM).**
#### :pushpin: Si les filaments ne peuvent pas être insérés dans les « tubes PTFE internes » de l'extrémité chaude M4V6, veuillez vous référer à ce guide ([:book: Comment remplacer les tubes PTFE internes](./ReplaceM4V6InnerPTFE.md)) pour remplacer les tubes PTFE internes bloqués.

### Pourquoi l'extrémité chaude est-elle bouchée ?
Certaines raisons peuvent entraîner le blocage de l'extrémité chaude, veuillez vérifier la liste une par une pour vous assurer que vous avez remarqué ces problèmes.
#### Étapes/méthodes incorrectes pour le chargement du filament
:pushpin: Lors du chargement du filament dans l'extrémité chaude, veuillez vous assurer que les filaments pénètrent par le bas de l'extrémité chaude.
:pushpin: Vous devez charger les 4 filaments dans l'extrémité chaude, que vous imprimiez des impressions 3D monochromes ou multicolores.
Pour savoir comment charger les filaments, veuillez vous référer à [:book: ce guide](#loadfilament) ou au [:clapper: tutoriel vidéo](https://youtu.be/-47yB95uIxI).
#### La buse est défectueuse
La buse peut également être partiellement obstruée. Si vous constatez que le filament qui s'écoule de la buse est plus fin que la normale, la buse peut être partiellement obstruée, veuillez remplacer directement une nouvelle buse.
#### La buse est trop proche de la plate-forme d'impression
Si la buse est trop proche du lit chaud lors de l'impression de la première couche, le filament peut ne pas être éjecté. Si cela se maintient pendant une longue période, cela peut entraîner une surcompression du filament dans l'extrémité chaude et provoquer un blocage (souvent bloqué à l'entrée de l'extrémité chaude). Lors de l'impression de la première couche, faites attention à la distance entre la buse et le lit chaud. Si nécessaire, ouvrez le menu « BabyStep » pour régler la hauteur de la buse.
#### Paramètre incorrect de « distance de rétraction du commutateur » dans les paramètres de coupe
Pour le hotend de couleur mixte 4-IN-1-OUT, la **« Longueur de rétraction de commutation de l'extrudeuse »** DOIT être réglée sur 0. Par exemple, définissez **« Distance de rétraction du commutateur de buse »** sur 0 dans Cura Slicer et définissez **« Rétraction lorsque l'outil est désactivé »** dans PrusaSlicer.
 

### :envelope: Si vous ne trouvez pas de solution pour résoudre votre problème après avoir lu la FAQ, veuillez contacter notre équipe d'assistance technique par [:e-mail:](support@zonestar3d.com) .

----
## <a id="de">So reinigen Sie das verstopfte M4V6-Hot-End</a> [:arrow_heading_up:](#choose-language)
- **Schritt 1: Erhitzen Sie die Düse auf 260 Grad.**
*Vorbereiten>>Filament>>Düse vorheizen: 260*, warten Sie, bis die Düse 260 Grad erreicht hat.
- **Schritt 2: Laden Sie alle 4 Filamente in das Hot-End.**
- **Schritt 3: Extrudieren Sie 4 Filamente gleichzeitig, bis Sie sehen, dass das Filament aus der Düse fließt.**
*Vorbereiten>>Filament>>Extruder: alle*
*Vorbereiten>>Filament>>langsam laden*, Sie müssen dies möglicherweise einige Male tun, bis alle 4 Filamente aus der Düse geflossen sind.
- **Schritt 4: 4 Filamente nacheinander extrudieren**
*Vorbereiten>>Filament>>Extruder: 1*    
*Vorbereiten>>Filament>>Extruder: langsam laden*, bis Sie sehen, dass das Filament von Extruder Nr. 1 aus der Düse fließt.    
*Vorbereiten>>Filament>>Extruder: 2*    
*Vorbereiten>>Filament>>Extruder: langsam laden*, bis Sie sehen, dass das Filament von Extruder Nr. 2 aus der Düse fließt.    
*Vorbereiten>>Filament>>Extruder: 3*    
*Vorbereiten>>Filament>>Extruder: langsam laden*, bis Sie sehen, dass das Filament von Extruder Nr. 3 aus der Düse fließt.    
*Vorbereiten>>Filament>>Extruder: 4*    
*Vorbereiten>>Filament>>Extruder: langsam laden*, bis Sie sehen, dass das Filament von Extruder Nr. 3 aus der Düse fließt.    
####
[Video-Tutorial](https://github.com/ZONESTAR3D/Z8P/assets/29502731/72312727-5ce5-4a35-8f2a-49f9145557ac)
#### :pushpin: Wenn das Hotend mit den oben genannten Schritten nicht gereinigt werden kann oder das Hotend nach der Reinigung immer noch leicht verstopft, entfernen Sie bitte die Düse und führen Sie die oben genannten Schritte erneut aus, um das Hotend zu reinigen, und installieren Sie dann eine neue Düse. Informationen zum Ersetzen einer Düse finden Sie in diesem **[:clapper: Video-Tutorial](https://youtu.be/L5VRyEbsJvM).**
#### :pushpin: Wenn die Filamente nicht in die „inneren PTFE-Röhrchen“ am M4V6-Hot-End eingesetzt werden können, lesen Sie bitte diese Anleitung ([:book: So ersetzen Sie die inneren PTFE-Röhrchen](./ReplaceM4V6InnerPTFE.md)), um die verstopften inneren PTFE-Röhrchen zu ersetzen.

### Warum ist das Hotend verstopft?
Es gibt einige Gründe, die dazu führen können, dass das Hotend verstopft ist. Bitte überprüfen Sie die Liste nacheinander, um sicherzustellen, dass Sie diese Probleme bemerkt haben.
#### Falsche Schritte/Methoden zum Laden des Filaments
:pushpin: Achten Sie beim Laden des Filaments in das Hotend darauf, dass die Filamente in die Unterseite des Hotends gelangen.
:pushpin: Sie müssen alle 4 Filamente in das Hotend laden, unabhängig davon, ob Sie ein- oder mehrfarbige 3D-Drucke drucken.
Informationen zum Laden von Filamenten finden Sie in [:book: dieser Anleitung](#loadfilament) oder im [:clapper: Video-Tutorial](https://youtu.be/-47yB95uIxI).
#### Düse ist defekt
Die Düse ist möglicherweise auch teilweise verstopft. Wenn Sie feststellen, dass das aus der Düse austretende Filament dünner als normal ist, ist die Düse möglicherweise teilweise verstopft. Bitte ersetzen Sie sie direkt durch eine neue Düse.
#### Die Düse ist zu nahe an der Druckplattform
Wenn die Düse beim Drucken der ersten Schicht zu nahe am Heizbett ist, wird das Filament möglicherweise nicht ausgeworfen. Wenn dies über einen längeren Zeitraum anhält, kann dies dazu führen, dass das Filament im Hotend überkomprimiert wird und eine Verstopfung verursacht (häufig am Eingang des Hotends verstopft). Achten Sie beim Drucken der ersten Schicht auf den Abstand zwischen der Düse und dem Heizbett. Öffnen Sie bei Bedarf das Menü „BabyStep“, um die Düsenhöhe anzupassen.
#### Falsche Einstellung für „Schalterrückzugsabstand“ in den Slice-Einstellungen
Für 4-IN-1-OUT-Mischfarb-Hotends MUSS die **„Extruder-Schalterrückzugslänge“** auf 0 eingestellt werden. Stellen Sie beispielsweise **„Düsenschalter-Rückzugsabstand“** in Cura Slicer auf 0 und **„Rückzug bei deaktiviertem Werkzeug“** in PrusaSlicer ein.
 

### :envelope: Wenn Sie nach dem Lesen der FAQ keine Lösung für Ihr Problem finden, wenden Sie sich bitte per [:e-mail:](support@zonestar3d.com) an unser technisches Supportteam.

----
## <a id="it">Come pulire l'hot end M4V6 intasato</a> [:arrow_heading_up:](#choose-language)
- **Passaggio 1: Riscaldare l'ugello a 260 gradi.**
*Preparare>>Filamento>>Preriscaldare l'ugello: 260*, attendere che l'ugello raggiunga i 260 gradi.
- **Passaggio 2: Caricare tutti e 4 i filamenti nell'hot end.**
- **Passaggio 3: Estrudere 4 filamenti contemporaneamente, finché non si vede il filamento uscire dall'ugello.**
*Preparare>>Filamento>>estrusore: tutto*
*Preparare>>Filamento>>caricare lentamente*, potrebbe essere necessario ripetere l'operazione più volte, finché tutti e 4 i filamenti non saranno usciti dall'ugello. - **Passaggio 4: estrudere 4 filamenti uno alla volta**
*Prepara>>Filamento>>estrusore: 1*    
*Prepara>>Filamento>>estrusore: caricare lentamente*, finché non vedi il filamento dell'estrusore n. 1 uscire dall'ugello.    
*Prepara>>Filamento>>estrusore: 2*    
*Prepara>>Filamento>>estrusore: caricare lentamente*, finché non vedi il filamento dell'estrusore n. 2 uscire dall'ugello.    
*Prepara>>Filamento>>estrusore: 3*    
*Prepara>>Filamento>>estrusore: caricare lentamente*, finché non vedi il filamento dell'estrusore n. 3 uscire dall'ugello.    
*Prepara>>Filamento>>estrusore: 4*    
*Prepara>>Filamento>>estrusore: carica lentamente*, finché non vedi il filamento dell'estrusore n. 3 uscire dall'ugello.    
####
[Video tutorial](https://github.com/ZONESTAR3D/Z8P/assets/29502731/72312727-5ce5-4a35-8f2a-49f9145557ac)
#### :pushpin: Se l'hot end non può essere pulito eseguendo i passaggi precedenti, o l'hot end si ostruisce ancora facilmente dopo la pulizia, rimuovi l'ugello e ripeti i passaggi precedenti per pulire nuovamente l'hotend, quindi installa un nuovo ugello. Per informazioni su come sostituire un ugello, guarda questo **[:clapper: video tutorial](https://youtu.be/L5VRyEbsJvM).**
#### :pushpin: Se i filamenti non possono essere inseriti nei "tubi interni in PTFE" dell'hot end M4V6, fai riferimento a questa guida ([:book: Come sostituire i tubi interni in PTFE](./ReplaceM4V6InnerPTFE.md)) per sostituire i tubi interni in PTFE bloccati.

### Perché l'hotend è intasato?
Ci sono alcuni motivi che possono causare il blocco dell'hotend, controlla l'elenco uno per uno per assicurarti di aver notato questi problemi.
#### Passaggi/metodi errati per caricare il filamento
:pushpin: Quando carichi il filamento nell'hotend, assicurati che i filamenti entrino nella parte inferiore dell'hotend. :pushpin: Devi caricare tutti e 4 i filamenti nell'hot end, sia che tu stia stampando stampe 3D monocolore o multicolore.
Per sapere come caricare i filamenti, fai riferimento a [:book: questa guida](#loadfilament) o al [:clapper: video tutorial](https://youtu.be/-47yB95uIxI).
#### L'ugello è difettoso
L'ugello potrebbe anche essere parzialmente ostruito. Se noti che il filamento che esce dall'ugello è più sottile del normale, l'ugello potrebbe essere parzialmente ostruito, sostituisci direttamente un nuovo ugello.
#### L'ugello è troppo vicino alla piattaforma di stampa
Se l'ugello è troppo vicino al letto caldo durante la stampa del primo strato, il filamento potrebbe non essere espulso. Se questa situazione persiste per molto tempo, potrebbe causare una compressione eccessiva del filamento nell'hot end e causare un blocco (spesso bloccato all'ingresso dell'hotend). Quando stampi il primo strato, fai attenzione alla distanza tra l'ugello e il letto caldo. Se necessario, apri il menu "BabyStep" per regolare l'altezza dell'ugello.
#### Impostazione errata "distanza di retrazione dell'interruttore" nelle impostazioni di slice
Per l'hotend a colori misti 4-IN-1-OUT, **"Lunghezza di retrazione dell'interruttore dell'estrusore"** DEVE essere impostata su 0. Ad esempio, imposta **"Distanza di retrazione dell'interruttore dell'ugello"** su 0 in Cura Slicer e imposta **"Retrazione quando l'utensile è disabilitato"** in PrusaSlicer.
 

### :envelope: Se non riesci a trovare una soluzione per risolvere il tuo problema dopo aver letto le FAQ, contatta il nostro team di supporto tecnico tramite [:e-mail:](support@zonestar3d.com).

----
## <a id="ru">Как очистить засоренный горячий конец M4V6</a> [:arrow_heading_up:](#choose-language)
- **Шаг 1: Нагрев сопла до 260 градусов.**
*Подготовка>>Нить>>Предварительный нагрев сопла: 260*, подождите, пока сопло достигнет 260 градусов.
- **Шаг 2: Загрузите все 4 нити в горячий конец.**
- **Шаг 3: Экструдер с 4 нитями одновременно, пока не увидите, что нить вытекает из сопла.**
*Подготовка>>Нить>>Экструдер: все*
*Подготовка>>Нить>>медленно загружайте*, вам может потребоваться сделать это несколько раз, пока все 4 нити не вытекут из сопла.
- **Шаг 4: Выдавите 4 нити одну за другой**
*Подготовка>>Нить>>Экструдер: 1*    
*Подготовка>>Нить>>Экструдер: медленно загружайте*, пока не увидите, что нить экструдера № 1 вытекает из сопла.    
*Подготовка>>Нить>>Экструдер: 2*    
*Подготовка>>Нить>>Экструдер: медленно загружайте*, пока не увидите, что нить экструдера № 2 вытекает из сопла.    
*Подготовка>>Нить>>Экструдер: 3*    
*Подготовка>>Нить>>Экструдер: медленно загружайте*, пока не увидите, что нить экструдера № 3 вытекает из сопла.    
*Подготовка>>Нить>>экструдера: 4*    
*Подготовка>>Нить>>экструдера: медленно загружайте*, пока не увидите, что нить экструдера № 3 вытекает из сопла.    
####
[Видеоурок](https://github.com/ZONESTAR3D/Z8P/assets/29502731/72312727-5ce5-4a35-8f2a-49f9145557ac)
#### :pushpin: Если горячий конец не удается очистить, выполнив указанные выше действия, или горячий конец по-прежнему легко засоряется после очистки, снимите сопло и выполните указанные выше действия еще раз, чтобы очистить горячий конец, а затем установите новое сопло. О том, как заменить сопло, посмотрите это **[:clapper: видеоруководство](https://youtu.be/L5VRyEbsJvM).**
#### :pushpin: Если нити не могут быть вставлены во «внутренние трубки PTFE» на хотэнде M4V6, обратитесь к этому руководству ([:book: Как заменить внутренние трубки PTFE](./ReplaceM4V6InnerPTFE.md)), чтобы заменить заблокированные внутренние трубки PTFE.

### Почему засоряется хотэнд?
Существует несколько причин, которые могут привести к блокировке хотэнда, пожалуйста, проверьте список одну за другой, чтобы убедиться, что вы заметили эти проблемы.
#### Неправильные шаги/методы загрузки нити
:pushpin: При загрузке нити в хотэнд убедитесь, что нити входят в нижнюю часть хотэнда.
:pushpin: Вам необходимо загрузить все 4 нити в хотэнд, независимо от того, печатаете ли вы одноцветные или многоцветные 3D-отпечатки.
О том, как загрузить нити, см. [:book: это руководство](#loadfilament) или [:clapper: видеоурок](https://youtu.be/-47yB95uIxI).
#### Сопло неисправно
Сопло также может быть частично засорено. Если вы обнаружите, что нить, выходящая из сопла, тоньше обычного, сопло может быть частично засорено, пожалуйста, замените сопло на новое.
#### Сопло расположено слишком близко к печатной платформе
Если сопло расположено слишком близко к горячему столу при печати первого слоя, нить может не выталкиваться. Если это будет продолжаться в течение длительного времени, это может привести к чрезмерному сжатию нити в хотэнде и вызвать закупорку (часто блокируется на входе в хотэнд). При печати первого слоя обратите внимание на расстояние между соплом и горячей платформой. При необходимости откройте меню «BabyStep», чтобы отрегулировать высоту сопла.
#### Неправильная настройка «расстояние отвода переключения» в настройках среза
Для 4-IN-1-OUT смешанного цветного горячего конца **«Длина отвода переключения экструдера»** ДОЛЖНА быть установлена на 0. Например, установите **«Расстояние отвода переключения сопла»** на 0 в Cura Slicer и установите **«Отвод при отключении инструмента»** в PrusaSlicer.
 

### :envelope: Если вы не можете найти решение для своей проблемы после прочтения FAQ, свяжитесь с нашей службой технической поддержки по [:e-mail:](support@zonestar3d.com) .

----
## <a id="jp">詰まった M4V6 ホットエンドのクリーニング方法</a> [:arrow_heading_up:](#choose-language)
- **ステップ 1: ノズルを 260 度に加熱します。**
*準備>>フィラメント>>ノズルを予熱: 260*、ノズルが 260 度に達するまで待ちます。
- **ステップ 2: 4 つのフィラメントすべてをホットエンドにロードします。**
- **ステップ 3: フィラメントがノズルから流れ出るのがわかるまで、4 つのフィラメントを同時に押し出します。**
*準備>>フィラメント>>押し出し: すべて*
*準備>>フィラメント>>ゆっくりロード*、4 つのフィラメントすべてがノズルから流れ出るまで、数回実行する必要がある場合があります。
- **ステップ 4: 4 本のフィラメントを 1 本ずつ押し出します**
*準備>>フィラメント>>押出機: 1*    
*準備>>フィラメント>>押出機: ゆっくりロード*、押出機 #1 のフィラメントがノズルから流れ出るのを確認するまで。    
*準備>>フィラメント>>押出機: 2*    
*準備>>フィラメント>>押出機: ゆっくりロード*、押出機 #2 のフィラメントがノズルから流れ出るのを確認するまで。    
*準備>>フィラメント>>押出機: 3*    
*準備>>フィラメント>>押出機: ゆっくりロード*、押出機 #3 のフィラメントがノズルから流れ出るのを確認するまで。    
*準備>>フィラメント>>押出機: 4*    
*準備>>フィラメント>>押出機: ゆっくりとロード*、押出機 #3 のフィラメントがノズルから流れ出るのを確認するまで。    
####
[ビデオチュートリアル](https://github.com/ZONESTAR3D/Z8P/assets/29502731/72312727-5ce5-4a35-8f2a-49f9145557ac)
#### :pushpin: 上記の手順を実行してもホットエンドをクリーニングできない場合、またはクリーニング後もホットエンドが詰まりやすい場合は、ノズルを取り外して上記の手順を 1 回実行し、ホットエンドを再度クリーニングしてから、新しいノズルを取り付けてください。ノズルの交換方法については、この**[:clapper: ビデオチュートリアル](https://youtu.be/L5VRyEbsJvM)をご覧ください。**
#### :pushpin: M4V6ホットエンドの「内側のPTFEチューブ」にフィラメントを挿入できない場合は、このガイド([:book: 内側のPTFEチューブの交換方法](./ReplaceM4V6InnerPTFE.md))を参照して、詰まった内側のPTFEチューブを交換してください。

### ホットエンドが詰まるのはなぜですか?
ホットエンドが詰まる原因はいくつかあります。リストを1つずつ確認して、これらの点に気付いていることを確認してください。
#### フィラメントをロードするための手順/方法が間違っている
:pushpin: フィラメントをホットエンドにロードするときは、フィラメントがホットエンドの底部に入るようにしてください。
:pushpin: 1 色または多色の 3D プリントを印刷する場合でも、4 つのフィラメントすべてをホット エンドにロードする必要があります。
フィラメントのロード方法については、[:book: このガイド](#loadfilament) または [:clapper: ビデオ チュートリアル](https://youtu.be/-47yB95uIxI) を参照してください。
#### ノズルに欠陥があります
ノズルが部分的に詰まっている可能性もあります。ノズルから流れ出たフィラメントが通常よりも細い場合は、ノズルが部分的に詰まっている可能性があります。新しいノズルを直接交換してください。
#### ノズルが印刷プラットフォームに近すぎます
最初のレイヤーを印刷するときにノズルがホット ベッドに近すぎると、フィラメントが排出されない場合があります。この状態が長時間続くと、ホット エンドのフィラメントが過度に圧縮され、詰まりが発生する可能性があります (多くの場合、ホットエンドの入口で詰まります)。最初のレイヤーを印刷するときは、ノズルとホットベッドの間の距離に注意してください。必要に応じて、「BabyStep」メニューを開いてノズルの高さを調整してください。
#### スライス設定の「スイッチ後退距離」設定が正しくありません
4-IN-1-OUT ミックスカラーホットエンドの場合、**「エクストルーダー切り替え後退長さ」** を 0 に設定する必要があります。たとえば、Cura Slicer で **「ノズルスイッチ後退距離」** を 0 に設定し、PrusaSlicer で **「ツールが無効のときの後退」** を設定します。
 

### :envelope: FAQ を読んでも問題の解決策が見つからない場合は、[:e-mail:](support@zonestar3d.com) でテクニカルサポートチームにお問い合わせください。

----
## <a id="kr">막힌 M4V6 핫엔드 청소 방법</a> [:arrow_heading_up:](#choose-language)
- **1단계: 노즐을 260도로 가열합니다.**
*준비>>필라멘트>>노즐 예열: 260*, 노즐이 260도에 도달할 때까지 기다립니다.
- **2단계: 모든 4개 필라멘트를 핫엔드에 로드합니다.**
- **3단계: 필라멘트가 노즐에서 흘러나오는 것을 볼 수 있을 때까지 4개 필라멘트를 동시에 압출합니다.**
*준비>>필라멘트>>압출기: 모두*
*준비>>필라멘트>>천천히 로드*, 4개 필라멘트가 모두 노즐에서 흘러나올 때까지 몇 번 해야 할 수도 있습니다.
- **4단계: 4개의 필라멘트를 하나씩 압출**
*준비>>필라멘트>>압출기: 1*    
*준비>>필라멘트>>압출기: 천천히 로드*하여 압출기 #1의 필라멘트가 노즐에서 흘러나오는 것을 볼 때까지.    
*준비>>필라멘트>>압출기: 2*    
*준비>>필라멘트>>압출기: 천천히 로드*하여 압출기 #2의 필라멘트가 노즐에서 흘러나오는 것을 볼 때까지.    
*준비>>필라멘트>>압출기: 3*    
*준비>>필라멘트>>압출기: 천천히 로드*하여 압출기 #3의 필라멘트가 노즐에서 흘러나오는 것을 볼 때까지.    
*준비>>필라멘트>>압출기: 4*    
*준비>>필라멘트>>압출기: 천천히 로드*하여 압출기 #3의 필라멘트가 노즐에서 흘러나오는 것을 볼 때까지.    
####
[비디오 튜토리얼](https://github.com/ZONESTAR3D/Z8P/assets/29502731/72312727-5ce5-4a35-8f2a-49f9145557ac)
#### :pushpin: 위의 단계를 수행해도 핫엔드를 청소할 수 없거나 청소 후에도 핫엔드가 쉽게 막히는 경우 노즐을 제거하고 위의 단계를 한 번 수행하여 핫엔드를 다시 청소한 다음 새 노즐을 설치하세요. 노즐을 교체하는 방법에 대해서는 이 **[:clapper: 비디오 튜토리얼](https://youtu.be/L5VRyEbsJvM)**을 시청하세요.
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

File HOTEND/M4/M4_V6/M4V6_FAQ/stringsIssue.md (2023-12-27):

## How to solve the stringing issue of M4V6
**Stringing issue**([:link:wiki](https://www.matterhackers.com/articles/3d-printer-troubleshooting-guide#Issue9)) is a common issue , especially for a FDM 3D printers that use **bowden type extruder** ([:link:wiki](https://en.wikipedia.org/wiki/3D_printer_extruder)).
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

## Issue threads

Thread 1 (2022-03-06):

extruder skipping steps

MKdent, 2022-03-06:
Hi, I do have the Z9v5_E4 board. After changing to direct drive update the extruder skips steps, for example if you do load filament fast...
Any adjustment in marlin conceringing this?

ZONESTAR3D, 2022-03-08:
font{
        line-height: 1.6;
    }
    ul,ol{
        padding-left: 20px;
        list-style-position: inside;
    }

        Dear,
        Thanks contact with us.You can change the steps/mm of extruder to correct it.1. If you have a ZONESTAR 3D printer, please tell me the model of your printer, I will provide the correct firmware to you.2. If you use this control board to your own 3d printer, please tell me more details  (as below) , I will tell you how to set the steps/mm of extruder.2-1. Extruder type :(for example Titan, BGM, etc.)2-2 Motor driver (A4988, TMC220x, TMC2225/6, etc.)Here is the setting in marlin source code (configuration.h):

            ZONESTAR online shopZONESTAR Innovations Tech., Ltd.
                                  ***@***.*** email: ***@***.***

    On 3/6/2022 ***@***.***> wrote：

Hi, I do have the Z9v5_E4 board. After changing to direct drive update the extruder skips steps, for example if you do load filament fast...
Any adjustment in marlin conceringing this?

—Reply to this email directly, view it on GitHub, or unsubscribe.You are receiving this because you are subscribed to this thread.Message ID: ***@***.***>

MKdent, 2022-03-08:
Hi,
I do have

Z9V5 Pro version 2 (probably  ZM3E4 board...with exturder stepper driver A4988.).

I uploaded firmware Z9V5_E4 and defined BMG Extruder. So steps/mm , I believe, are actually adjusted right....

I did also manually changed them over display. And same thing happenend. loading filament fast and motor skips steps.

So I believe motor has not enough torque?
Are there any adjustements to be made for stepper driver current?

ZONESTAR3D, 2022-03-08:
font{
        line-height: 1.6;
    }
    ul,ol{
        padding-left: 20px;
        list-style-position: inside;
    }

        Hi Friend,
        I think your printer model is Z9V5Pro-MK2, you can refer to the below link to know more details of these model.https://github.com/ZONESTAR3D/Z9/tree/main/Z9V5 Firmware Download link for Z9V5Pro-MK2:https://github.com/ZONESTAR3D/Firmware/tree/master/Z9/Z9V5/bin/Z9V5Pro/released

            ZONESTAR online shopZONESTAR Innovations Tech., Ltd.
                                  ***@***.*** email: ***@***.***

    On 3/8/2022 ***@***.***> wrote：

    font{
        line-height: 1.6;
    }
    ul,ol{
        padding-left: 20px;
        list-style-position: inside;
    }

        Dear,
        Thanks contact with us.You can change the steps/mm of extruder to correct it.1. If you have a ZONESTAR 3D printer, please tell me the model of your printer, I will provide the correct firmware to you.2. If you use this control board to your own 3d printer, please tell me more details  (as below) , I will tell you how to set the steps/mm of extruder.2-1. Extruder type :(for example Titan, BGM, etc.)2-2 Motor driver (A4988, TMC220x, TMC2225/6, etc.)Here is the setting in marlin source code (configuration.h):

            ZONESTAR online shopZONESTAR Innovations Tech., Ltd.
                                  ***@***.*** email: ***@***.***

    On 3/6/2022 ***@***.***> wrote：

Hi, I do have the Z9v5_E4 board. After changing to direct drive update the extruder skips steps, for example if you do load filament fast...
Any adjustment in marlin conceringing this?

—Reply to this email directly, view it on GitHub, or unsubscribe.You are receiving this because you are subscribed to this thread.Message ID: ***@***.***>

MKdent, 2022-03-09:
Thanks for helping! I tried your firmware but it's the same. It feels like the extruder motor has not enough torque or power...

ZONESTAR3D, 2022-03-10:
font{
        line-height: 1.6;
    }
    ul,ol{
        padding-left: 20px;
        list-style-position: inside;
    }

        Hi Friend,
        Please take a photo to me about the serial number of your kit, you can find a white label pasted on the power supply.And please take a photo to show the firmware version too: LCD MENU>>Info>>I will help to check.PS: If possible, please take a small video to show what's question you have and send it to me.

            ZONESTAR online shopZONESTAR Innovations Tech., Ltd.
                                  ***@***.*** email: ***@***.***

    On 3/8/2022 ***@***.***> wrote：

Hi,
I do have
Z9V5 Pro version 2 (probably  ZM3E4 board...with exturder stepper driver A4988.).
I uploaded firmware Z9V5_E4 and defined BMG Extruder. So steps/mm , I believe, are actually adjusted right....
I did also manually changed them over display. And same thing happenend. loading filament fast and motor skips steps.
So I believe motor has not enough torque?
Are there any adjustements to be made for stepper driver current?

—Reply to this email directly, view it on GitHub, or unsubscribe.You are receiving this because you commented.Message ID: ***@***.***>

MKdent, 2022-03-10:
Hi,
you find the pictures of firmware and versions below.
I uploaded a video. Hope you can see it. https://youtu.be/1vfw2IVoRfE
The extruder is working fine when  slow motion is required. But when it should load filament fast the stepper motor is not powerful enough and cannot move the white gear ( See menu prepare->filament->laod quickly). I think it also has an negativ  effect on normal printing.

Hope you know a solution.

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

ZONESTAR3D, 2022-03-11:
font{
        line-height: 1.6;
    }
    ul,ol{
        padding-left: 20px;
        list-style-position: inside;
    }

        Hi,
        1. please note "Quickly Load" only work when loading filament from the extruder to the hotend, it should not be used when filaments have entered the hot end.2. please follow this link to check if the extruders installed well and try to increase the pressure of the extrudee by adjust the srews.

            ZONESTAR online shopZONESTAR Innovations Tech., Ltd.
                                  ***@***.*** email: ***@***.***

    On 3/11/2022 ***@***.***> wrote：

Hi,
you find the pictures of firmware and versions below.
I uploaded a video. Hope you can see it. https://youtu.be/1vfw2IVoRfE
The extruder is working fine when  slow motion is required. But when it should load filament fast the stepper motor is not powerful enough and cannot move the white gear ( See menu prepare->filament->laod quickly). I think it also has an negativ  effect on normal printing.
Hope you know a solution.

—Reply to this email directly, view it on GitHub, or unsubscribe.You are receiving this because you commented.Message ID: ***@***.***>

MKdent, 2022-03-18:
"Quickly Load" only work when loading filament from the extruder to the hotend, it should not be used when filaments have entered the hot end.

I wasn't aware of that. So kept on going and I was able to print.  Thanks for the info.
Meanwhile another problem occured for which I opend another issue. Maybe you have a look at this.

Closed 2022-03-18.

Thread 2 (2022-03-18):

Without active bed leveling, printing is fine but when it comes to active bed leveling strange movement.....

MKdent, 2022-03-18:
Another problem occured with the zl-sensor. Bed leveling does work fine but when it comes to printing with active bed leveling (M420 S1) the extruder shifts x and y position somehow.  It's printing like concentric circles ( at the beginnin when the brim should be printed) and even prints outside the bed. I'm using the normal firmware source code but do activate active bed leveling with M420 S1.

This is my cura start code:

G28 ; home all axes
G29
M500
M420 S1
G1 Z5 F3000 ; lift
G1 X5 Y10 F1500 ; move to prime
G1 Z0.2 F3000 ; get ready to prime
G92 E0 ; reset extrusion distance
G1 Y80 E10 F600 ; prime nozzle
G1 Y100 F5000 ; quick wipe

Any idea?

Closed 2022-09-23.

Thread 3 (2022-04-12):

Unified Bed Leveling

gpwestern78, 2022-04-12:
Have a Z8T that I upgraded to use zm3e4 (v 1.0) board, the Zonestar wifi module (from Zonestar _official store on AliExpress,) 2208 steppers for all motors, and LCDDWIN (from same store) and using firmware source from this repository I am unable to compile after commenting out bilinear bed leveling and enabling unified bed leveling options.

ZONESTAR3D, 2022-09-23:
Please download the new firmware source code and build it again, thanks!

Closed 2022-09-23.

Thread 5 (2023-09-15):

Replace the inner PTFE tubes for M4V6 hotend

ZONESTAR3D, 2023-09-15:
A video tutorial for replacing the inner PTFE tubes of the M4V6 hotend...

Closed 2023-09-15.

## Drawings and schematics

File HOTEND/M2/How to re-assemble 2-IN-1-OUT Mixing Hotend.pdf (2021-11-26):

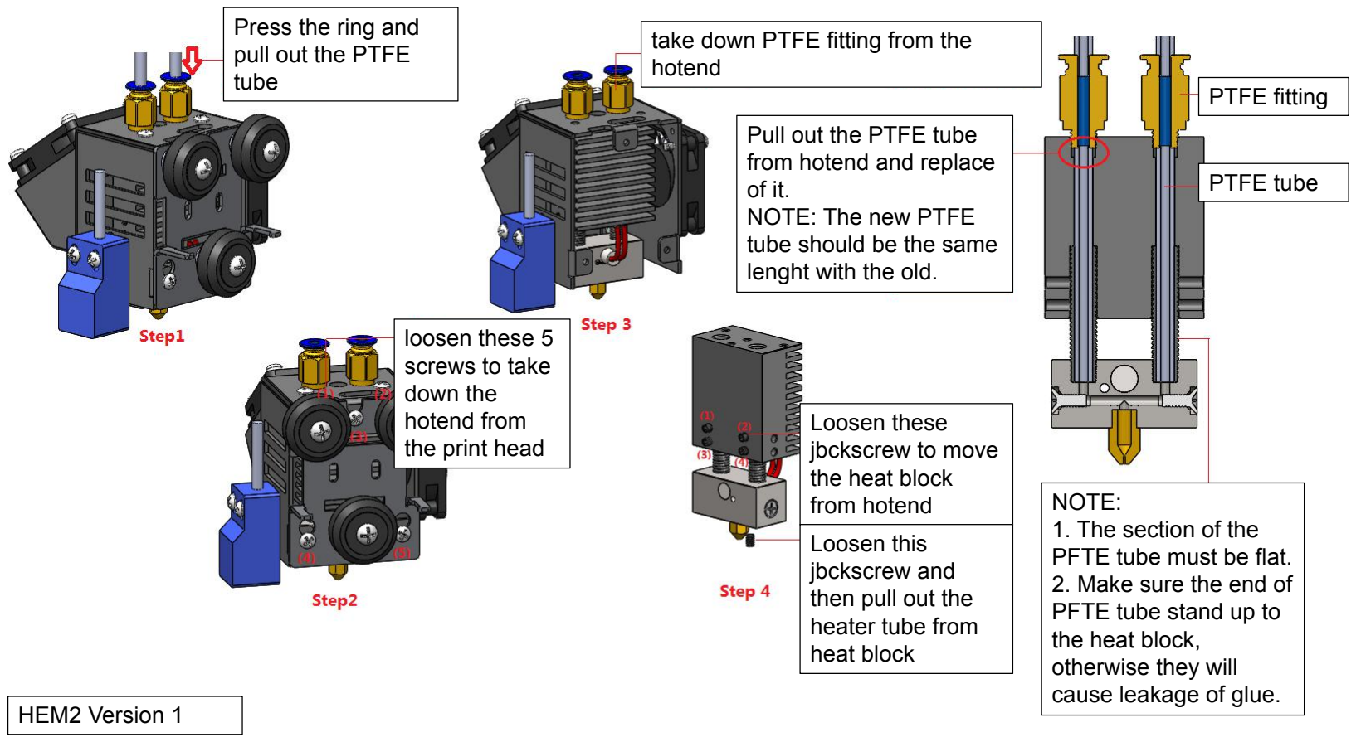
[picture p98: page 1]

Press the ring and
pull out the PTFE
tube

take down PTFE fitting from the hotend

loosen these 5
screws to take
down the
hotend from
the print head

Loosen these
jbckscrew to move
the heat block
from hotend
Loosen this
jbckscrew and
then pull out the
heater tube from
heat block

Pull out the PTFE tube
from hotend and replace
of it. NOTE: The new PTFE

tube should be the same
lenght with the old. | NOTE:
1. The section of the
PFTE tube must be flat. 2. Make sure the end of

PFTE tube stand up to
the heat block, otherwise they will

cause leakage of glue.

PTFE fitting

PTFE tube

HEM2 Version 1

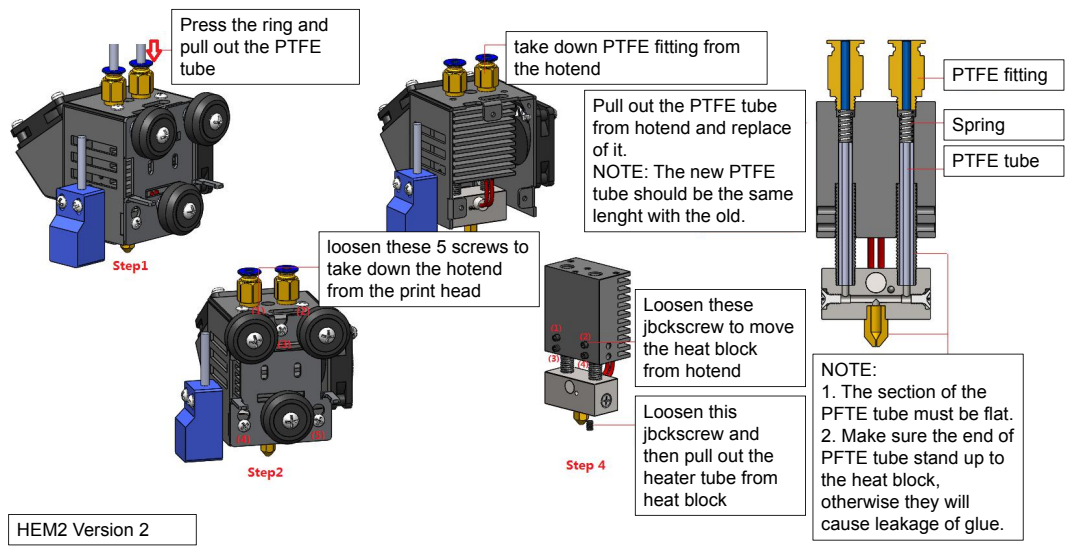
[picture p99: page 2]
lenght with the old.; NOTE:; PTFE fitting; Spring; PTFE tube; HEM2 Version 2

Press the ring and
pull out the PTFE
tube

take down PTFE fitting from
the hotend

Pull out the PTFE tube
from hotend and replace
of it. NOTE: The new PTFE
tube should be the same

loosen these 5 screws to
take down the hotend
from the print head

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

1. The section of the
PFTE tube must be flat. 2. Make sure the end of
PFTE tube stand up to
the heat block, otherwise they will
cause leakage of glue.

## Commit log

2021-10-25 add E4 Fanduck stl file
    [fan_duck_e4_v1.stl]
2021-10-28 add DDE bracket metal piece drawing file
    [DDE_BR_V1.stl]
2021-10-28 updata DDE_BR_V1 3d drawing
    [DDE_BR_V1.igs]
2021-11-04 updata in 2021-11-04
    [HM3_V2.igs, HM3_V2.stl, HM3_V2.stp]
2021-11-26 add DDE 3d drawing
    [tpuext_v3_asm.stp]
2021-11-26 add fan duck stl file
    [fan_duck_m4_v3.stl]
2021-11-28 add M4-V5 user guide
    [HOUSING_M4_V3.stp, fan_duck_m4_v3.stl, fan_m4_v1.stl]
2021-12-03 add E4 printing sample
    [E4_PhoneBracket.3mf, E4_Retraction_Test.3mf]
2021-12-03 updata E4 printing sample
    [E4_PhoneBracket.3mf]
2021-12-04 updata in 2021-12-04
    [ZZ_tft35_mk_case_a.3mf, ZZ_tft35_mk_case_b.3mf, mks_config.txt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]
2021-12-04 updata .gitignore
    [mks_config.txt]
2021-12-06 add test example for E4 hotend
    [4C_Niko_Dog_2.stl, 4C_Niko_Dog_3.stl, 4C_Niko_Dog_4.stl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]
2021-12-06 updata E4 test file
    [Z9E4_4Color_Test.3mf]
2021-12-06 add readme file
    [fan_duck_e4_v1.stl]
2021-12-07 updata E4 hotend example
    [M4_4C_Test.3mf]
2021-12-07 updata M4 example
    [M4_4C_Test.3mf]
2021-12-07 updata in 2021-12-07
    [E4_PhoneBracket.3mf]
2021-12-08 updata R3 hotend
    [HM3_V2.igs, HM3_V2.stl, HM3_V2.stp]
2021-12-09 updata readme
    [M4_1C_PhoneBracket.3mf, Z9_phone_bracket.stl]
2021-12-11 updata example for M4 hotend
    [M4_Retraction_Test.3mf]
2021-12-13 updata E4 unassemble guide
    [M4_1C_PhoneBracket.3mf, Z9_phone_bracket.stl, phone_bracket.stl]
2021-12-16 updata M4
    [Belly.stl, Ears.stl, Eyebrow.stl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]
2022-01-03 add ARPM
    [Belly.stl, Ears.stl, Eyebrow.stl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]
2022-01-08 updata repeat printing firmware for Z9V5
2022-01-10 updata user guide for mixing color hotend
2022-01-30 updata wiring for ARPM
2022-03-07 updata WiFi readme
    [T5UIC1.CFG]
2022-04-08 Update Retraction Test example
    [M4_Retraction_Test.3mf]
2022-04-13 update hotend readme file
2022-04-22 update slicing excmple for E4 hotend
    [Z9E4_4C_Test.3mf]
2022-04-23 Update E4 example
    [Z9E4_4Color_Test.3mf]
2022-04-24 update E4 example by PrusaSlicer
    [Color_1.stl, Color_2.stl, Color_3.stl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]
2022-04-26 update bdd
    [Z9E4_BDD_0424.3mf]
2022-04-26 change fan speed
2022-05-11 update E4 printing examples
2022-05-16 update Cura Slicing Setting for E4 hotend
2022-05-26 update solutions for M4 hotend
2022-05-30 update in 220530
    [fan_duck_e4_v2.stl]
2022-06-10 update single color hotend
    [FAN_PHS.stl, FAN_PHS_HF.stl, FAN_PHS_Z6.stl]
2022-06-16 update E4 gcode file
    [fan_duck_e4_v3.stl, fanduck_e4_5015.obj]
2022-07-06 update DWIN LCD MENU V3
    [T5UIC1.CFG, fan_duck_e4_v3.stl]
2022-07-07 updata readme for E4 hotend
2022-07-08 updata readme for DDE
    [DDE_BR_V1.stl, ENDSTOP_TG_Z6.stl, TPUEXT_PC_V0.stl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]
2022-07-27 updata readme for hotend
2022-08-16 add introduction of M4V6
    [fan_m4v6_v2.stl]
2022-09-20 updata readme for M4 hotend
2022-09-20 updata readme hotend
2022-09-23 updata user guide of E4 hotend
2022-09-23 updata M4V6 hotend
2022-10-05 update picture of E4 hotend
2022-10-05 update guide of E4 hotend
2022-10-22 fix links
    [Z9E4_BDD_0429.3mf]
2022-10-24 update E4 wiring
2022-11-01 add a principle video for E4 hotend
2022-11-28 update bed auto leveling guide
    [5500mW_v2.blend, BLtouch_Bracket.STL, DDE_BR_V1.igs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]
2022-11-29 upload DDE stl files
2023-01-05 update M4V6 high speed print guide
2023-01-14 updata readme of hotend
2023-02-07 update TFT-LCD
    [T5UIC1.CFG]
2023-02-28 upgrade readme
    [5500mW_v2.blend, For P802N P802M.STL, For old version D805.STL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]
2023-04-01 update laser guide
2023-04-03 update laser use guide
2023-04-13 update hotend documents
2023-04-17 update readme of M4 hotend
2023-05-20 update Z9V5 500x500 upgrade kit guide
    [br_hecable.stl]
2023-11-01 update user guide for E4 Hotend
2023-12-28 update user guide for upgrading dual gear extruder
2024-10-31 upload stl file
    [5015FAN_S.stl, 5015fan1.stl, FanDuct_4010B_M4V1.stl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]
2024-12-31 update wiring diagram
